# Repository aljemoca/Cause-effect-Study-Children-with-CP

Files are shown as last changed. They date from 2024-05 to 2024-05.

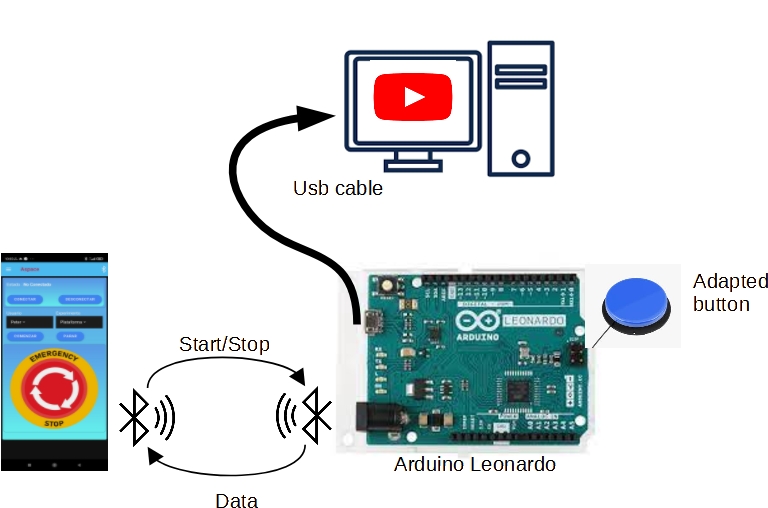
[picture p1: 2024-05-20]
Computer/AdaptedApplication.jpg

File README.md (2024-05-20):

# Cause-effect Study

 This project  contains the files needed to replicate all the elements (hardware/software) used to conduct an experiment to know the effect of mobility
 on cognitive skills in children with cerebral palsy. 

 Three main components are needed in this project:
 1) Platform (Explorer) that can be attached to a manual wheelchair and that can be operated by an adapted push button.
 2) A hardware that allows collecting data from typical cause-effect therapy programs. It consists of an Arduino-based switch-contrelled circuit that can control how long a video is played on a computer screen.
 3) A mobile application that allows controlling both hardware and collecting data for analysis.

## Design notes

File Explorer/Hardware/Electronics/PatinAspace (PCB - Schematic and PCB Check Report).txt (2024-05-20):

Schematic and PCB Check Report
------------------------------

Report Written:     Friday, May 28, 2021
Project Path:       C:\Users\ATC\Desktop\DISEÑO_PCB\DISEÑO_PCB\PatinAspace\PatinAspace.prj
Design Path:        C:\Users\ATC\Desktop\DISEÑO_PCB\DISEÑO_PCB\PatinAspace\PatinAspace.pcb
Design Title:       
Created:            25/05/2021 8:12:04
Last Saved:         28/05/2021 13:52:27
Editing Time:       4660 min
Units:              mm (precision 2)

Checking integrity of Schematic "C:\Users\ATC\Desktop\DISEÑO_PCB\DISEÑO_PCB\PatinAspace\PatinAspace.sch" with PCB "C:\Users\ATC\Desktop\DISEÑO_PCB\DISEÑO_PCB\PatinAspace\PatinAspace.pcb"
==========================================================================================================================================================================================

End Of Report.

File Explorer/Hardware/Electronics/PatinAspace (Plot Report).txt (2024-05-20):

Plot Report
-----------

Report Written:     Wednesday, November 24, 2021
Project Path:       C:\Users\ATC\Desktop\DISEÑO_PCB\DISEÑO_PCB\PatinAspace\PatinAspace.prj
Design Path:        C:\Users\ATC\Desktop\DISEÑO_PCB\DISEÑO_PCB\PatinAspace\PatinAspace.pcb
Design Title:       
Created:            25/05/2021 7:12:04
Last Saved:         02/06/2021 12:55:14
Editing Time:       4994 min
Units:              mm (precision 2)

Device Settings
===============

Gerber Settings
===============

    Leading zero suppression.
    G01 assumed throughout.
    Line termination <*> <CR> <LF>.
    3.5 format absolute inches.

    Format commands defined in Gerber file.
    Aperture table defined in Gerber file.
    Hardware arcs allowed.

Drill Settings
==============

    Excellon Format 2
    Format 3.5 absolute in mm.
    Zero suppression Leading

Plots Output
============

Gerber Output
=============

C:\Users\ATC\Desktop\DISEÑO_PCB\DISEÑO_PCB\PatinAspace\PatinAspace - Top Silkscreen.gbr

    Layers:
    ------------------
    Top Silkscreen

    D-Code Shape  (thou)
    -----------------------
    D12    Round 5.00
    D19    Round 12.00
    D22    Round 3.94

Gerber Output
=============

C:\Users\ATC\Desktop\DISEÑO_PCB\DISEÑO_PCB\PatinAspace\PatinAspace - Top Copper.gbr

    Layers:
    --------------
    Top Copper

    D-Code Shape  (thou)
    -------------------------------------------------------------
    D10    Round 11.81
    D13    Rounded Rectangle 60.00 X 60.00 X 0.00  Rotation 90
    D23    Round 25.20
    D24    Round 51.18
    D25    Round 15.00
    D78    Round 55.91
    D82    Round 60.00
    D99    Rectangle 60.00 X 60.00
    D100   Square 60.00

Gerber Output
=============

C:\Users\ATC\Desktop\DISEÑO_PCB\DISEÑO_PCB\PatinAspace\PatinAspace - Top Copper (Resist).gbr

    Layers:
    --------------
    Top Copper

    D-Code Shape  (thou)
    -------------------------------------------------------------
    D15    Rounded Rectangle 60.00 X 60.00 X 0.00  Rotation 90
    D91    Round 70.00
    D101   Rectangle 70.00 X 70.00
    D102   Square 70.00

Gerber Output
=============

C:\Users\ATC\Desktop\DISEÑO_PCB\DISEÑO_PCB\PatinAspace\PatinAspace - Top Copper (Paste).gbr

    Layers:
    --------------
    Top Copper

    D-Code Shape  (thou)
    -----------------------

Gerber Output
=============

C:\Users\ATC\Desktop\DISEÑO_PCB\DISEÑO_PCB\PatinAspace\PatinAspace - Bottom Copper.gbr

    Layers:
    -----------------
    Bottom Copper

    D-Code Shape  (thou)
    -------------------------------------------------------------
    D13    Rounded Rectangle 60.00 X 60.00 X 0.00  Rotation 90
    D23    Round 25.20
    D24    Round 51.18
    D25    Round 15.00
    D78    Round 55.91
    D82    Round 60.00
    D99    Rectangle 60.00 X 60.00
    D100   Square 60.00

Gerber Output
=============

C:\Users\ATC\Desktop\DISEÑO_PCB\DISEÑO_PCB\PatinAspace\PatinAspace - Bottom Copper (Resist).gbr

    Layers:
    -----------------
    Bottom Copper

    D-Code Shape  (thou)
    -------------------------------------------------------------
    D15    Rounded Rectangle 60.00 X 60.00 X 0.00  Rotation 90
    D91    Round 70.00
    D101   Rectangle 70.00 X 70.00
    D102   Square 70.00

Gerber Output
=============

C:\Users\ATC\Desktop\DISEÑO_PCB\DISEÑO_PCB\PatinAspace\PatinAspace - Bottom Copper (Paste).gbr

    Layers:
    -----------------
    Bottom Copper

    D-Code Shape  (thou)
    -----------------------

NC Drill Output
===============

C:\Users\ATC\Desktop\DISEÑO_PCB\DISEÑO_PCB\PatinAspace\PatinAspace - Drill Data - [Through Hole].drl

    Output:
    ---------------------------
    Plated Round Drill Holes
    Plated Slots

    Tool  Size       Count   ID
    ----------------------------------
    T001  0.40000 mm 31    E
    T002  0.70000 mm 48    G
    T003  0.80000 mm 76    F
    T004  0.85000 mm 68    B
    ----------------------------------
    Total            223
    ----------------------------------

C:\Users\ATC\Desktop\DISEÑO_PCB\DISEÑO_PCB\PatinAspace\PatinAspace - Drill Data - [Through Hole] (Unplated).drl

    Output:
    -----------------------------
    Unplated Round Drill Holes
    Unplated Slots

    Tool  Size Count   ID
    ----------------------------
    ----------------------------
    Total      0
    ----------------------------

Gerber Output
=============

C:\Users\ATC\Desktop\DISEÑO_PCB\DISEÑO_PCB\PatinAspace\PatinAspace - Drill Ident Drawing - [Through Hole].gbr

    Layers:
    ------------------
    [Through Hole]

Drill Ident Drawing
===================

    Drill Plated Size Shape ID
    -----------------------------------
    33    Y      100  Round B
    16    Y      100  Round E
    31    Y      100  Round F
    28    Y      100  Round G

    D-Code Shape  (thou)
    -----------------------
    D12    Round 5.00
    D18    Round 100.00

Gerber Output
=============

C:\Users\ATC\Desktop\DISEÑO_PCB\DISEÑO_PCB\PatinAspace\PatinAspace - board.gbr

    Layers:
    ------------------
    Board Outlines

    D-Code Shape  (thou)
    -----------------------
    D12    Round 5.00

Gerber Output
=============

C:\Users\ATC\Desktop\DISEÑO_PCB\DISEÑO_PCB\PatinAspace\PatinAspace - Botton Silkscreen.gbr

    Layers:
    ---------------------
    Bottom Silkscreen

    D-Code Shape  (thou)
    -----------------------

End Of Report.

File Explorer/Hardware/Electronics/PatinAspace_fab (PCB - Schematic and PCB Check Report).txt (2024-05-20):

Schematic and PCB Check Report
------------------------------

Report Written:     Thursday, June 10, 2021
Project Path:       C:\Users\ATC\Desktop\DISEÑO_PCB\DISEÑO_PCB\PatinAspace\PatinAspace_fab.prj
Design Path:        C:\Users\ATC\Desktop\DISEÑO_PCB\DISEÑO_PCB\PatinAspace\PatinAspace_fab.pcb
Design Title:       
Created:            25/05/2021 8:12:04
Last Saved:         10/06/2021 10:33:57
Editing Time:       5054 min
Units:              mm (precision 2)

Checking integrity of Schematic "C:\Users\ATC\Desktop\DISEÑO_PCB\DISEÑO_PCB\PatinAspace\PatinAspace_fab.sch" with PCB "C:\Users\ATC\Desktop\DISEÑO_PCB\DISEÑO_PCB\PatinAspace\PatinAspace_fab.pcb"
==================================================================================================================================================================================================

The PCB and Schematic designs do not match.
To bring them into line, you will need to make the following changes to the PCB design:

Component 'HC-SR04-CONNECTOR' package 'DIL' in PCB is newer version than Schematic, use Update Component to correct this.
Component '2WP' package 'DSC' in PCB is newer version than Schematic, use Update Component to correct this.

End Of Report.

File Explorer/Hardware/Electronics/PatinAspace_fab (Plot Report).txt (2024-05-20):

Plot Report
-----------

Report Written:     Thursday, July 08, 2021
Project Path:       C:\Users\ATC\Desktop\DISEÑO_PCB\DISEÑO_PCB\PatinAspace\PatinAspace_fab.prj
Design Path:        C:\Users\ATC\Desktop\DISEÑO_PCB\DISEÑO_PCB\PatinAspace\PatinAspace_fab.pcb
Design Title:       
Created:            25/05/2021 8:12:04
Last Saved:         18/06/2021 12:55:20
Editing Time:       5095 min
Units:              mm (precision 2)

Device Settings
===============

Gerber Settings
===============

    Leading zero suppression.
    G01 assumed throughout.
    Line termination <*> <CR> <LF>.
    3.5 format absolute inches.

    Format commands defined in Gerber file.
    Aperture table defined in Gerber file.
    Hardware arcs allowed.

Drill Settings
==============

    Excellon Format 2
    Format 3.5 absolute in mm.
    Zero suppression Leading

Plots Output
============

Gerber Output
=============

C:\Users\ATC\Desktop\DISEÑO_PCB\DISEÑO_PCB\PatinAspace\PatinAspace_fab - Top Silkscreen.gbr

    Layers:
    ------------------
    Top Silkscreen

    D-Code Shape  (thou)
    -----------------------
    D10    Round 11.81
    D12    Round 5.00
    D19    Round 12.00
    D22    Round 3.94

Gerber Output
=============

C:\Users\ATC\Desktop\DISEÑO_PCB\DISEÑO_PCB\PatinAspace\PatinAspace_fab - Top Copper.gbr

    Layers:
    --------------
    Top Copper

    D-Code Shape  (thou)
    -------------------------------------------------------------
    D23    Round 25.20
    D24    Round 51.18
    D25    Round 15.00
    D26    Rounded Rectangle 59.06 X 59.06 X 0.00  Rotation 90
    D27    Rectangle 59.06 X 59.06
    D28    Round 59.06
    D29    Square 59.06

Gerber Output
=============

C:\Users\ATC\Desktop\DISEÑO_PCB\DISEÑO_PCB\PatinAspace\PatinAspace_fab - Top Copper (Resist).gbr

    Layers:
    --------------
    Top Copper

    D-Code Shape  (thou)
    -------------------------------------------------------------
    D72    Rounded Rectangle 59.06 X 59.06 X 0.00  Rotation 90
    D73    Rectangle 69.06 X 69.06
    D74    Round 69.06
    D75    Square 69.06

Gerber Output
=============

C:\Users\ATC\Desktop\DISEÑO_PCB\DISEÑO_PCB\PatinAspace\PatinAspace_fab - Top Copper (Paste).gbr

    Layers:
    --------------
    Top Copper

    D-Code Shape  (thou)
    -----------------------

Gerber Output
=============

C:\Users\ATC\Desktop\DISEÑO_PCB\DISEÑO_PCB\PatinAspace\PatinAspace_fab - Bottom Copper.gbr

    Layers:
    -----------------
    Bottom Copper

    D-Code Shape  (thou)
    -------------------------------------------------------------
    D12    Round 5.00
    D23    Round 25.20
    D24    Round 51.18
    D25    Round 15.00
    D26    Rounded Rectangle 59.06 X 59.06 X 0.00  Rotation 90
    D27    Rectangle 59.06 X 59.06
    D28    Round 59.06
    D29    Square 59.06
    D76    Round 10.00

Gerber Output
=============

C:\Users\ATC\Desktop\DISEÑO_PCB\DISEÑO_PCB\PatinAspace\PatinAspace_fab - Bottom Copper (Resist).gbr

    Layers:
    -----------------
    Bottom Copper

    D-Code Shape  (thou)
    -------------------------------------------------------------
    D72    Rounded Rectangle 59.06 X 59.06 X 0.00  Rotation 90
    D73    Rectangle 69.06 X 69.06
    D74    Round 69.06
    D75    Square 69.06

Gerber Output
=============

C:\Users\ATC\Desktop\DISEÑO_PCB\DISEÑO_PCB\PatinAspace\PatinAspace_fab - Bottom Copper (Paste).gbr

    Layers:
    -----------------
    Bottom Copper

    D-Code Shape  (thou)
    -----------------------

NC Drill Output
===============

C:\Users\ATC\Desktop\DISEÑO_PCB\DISEÑO_PCB\PatinAspace\PatinAspace_fab - Drill Data - [Through Hole].drl

    Output:
    ---------------------------
    Plated Round Drill Holes
    Plated Slots

    Tool  Size       Count   ID
    ----------------------------------
    T001  0.60000 mm 33    D
    T002  0.80000 mm 124   F
    T003  0.90000 mm 16    H
    T004  1.02000 mm 52    I
    ----------------------------------
    Total            225
    ----------------------------------

C:\Users\ATC\Desktop\DISEÑO_PCB\DISEÑO_PCB\PatinAspace\PatinAspace_fab - Drill Data - [Through Hole] (Unplated).drl

    Output:
    -----------------------------
    Unplated Round Drill Holes
    Unplated Slots

    Tool  Size Count   ID
    ----------------------------
    ----------------------------
    Total      0
    ----------------------------

Gerber Output
=============

C:\Users\ATC\Desktop\DISEÑO_PCB\DISEÑO_PCB\PatinAspace\PatinAspace_fab - Drill Ident Drawing - [Through Hole].gbr

    Layers:
    ------------------
    [Through Hole]

Drill Ident Drawing
===================

    Drill Plated Size Shape ID
    -----------------------------------
    24    Y      100  Round D
    31    Y      100  Round F
    35    Y      100  Round H
    40    Y      100  Round I

    D-Code Shape  (thou)
    -----------------------
    D12    Round 5.00
    D18    Round 100.00

Gerber Output
=============

C:\Users\ATC\Desktop\DISEÑO_PCB\DISEÑO_PCB\PatinAspace\PatinAspace_fab - board_outline.gbr

    Layers:
    ------------------
    Board Outlines

    D-Code Shape  (thou)
    -----------------------
    D12    Round 5.00

End Of Report.

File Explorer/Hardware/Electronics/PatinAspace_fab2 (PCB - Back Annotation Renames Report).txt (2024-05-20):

Back Annotation Renames Report
------------------------------

Report Written:     Thursday, June 23, 2022
Project Path:       C:\Users\ATC\Desktop\DISEÑO_PCB\DISEÑO_PCB\PatinAspace2\PatinAspace_fab.prj
Design Path:        C:\Users\ATC\Desktop\DISEÑO_PCB\DISEÑO_PCB\PatinAspace2\PatinAspace_fab2.pcb
Design Title:       
Created:            25/05/2021 8:12:04
Last Saved:         23/06/2022 11:40:32
Editing Time:       6887 min
Units:              mm (precision 2)

Outstanding PCB renames awaiting back annotation to the Schematics design.

Rename Net from "enaRight" to "enaLeft1".
Rename Net from "enaLeft" to "enaRight".
Rename Net from "enaLeft1" to "enaLeft".

End Of Report.

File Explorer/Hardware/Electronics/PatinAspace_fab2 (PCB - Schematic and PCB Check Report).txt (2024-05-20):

Schematic and PCB Check Report
------------------------------

Report Written:     Thursday, June 23, 2022
Project Path:       C:\Users\ATC\Desktop\DISEÑO_PCB\DISEÑO_PCB\PatinAspace2\PatinAspace_fab.prj
Design Path:        C:\Users\ATC\Desktop\DISEÑO_PCB\DISEÑO_PCB\PatinAspace2\PatinAspace_fab2.pcb
Design Title:       
Created:            25/05/2021 8:12:04
Last Saved:         23/06/2022 11:47:56
Editing Time:       6896 min
Units:              mm (precision 2)

Checking integrity of Schematic "C:\Users\ATC\Desktop\DISEÑO_PCB\DISEÑO_PCB\PatinAspace2\PatinAspace_fab2.sch" with PCB "C:\Users\ATC\Desktop\DISEÑO_PCB\DISEÑO_PCB\PatinAspace2\PatinAspace_fab2.pcb"
======================================================================================================================================================================================================

The PCB and Schematic designs do not match.
To bring them into line, you will need to make the following changes to the PCB design:

Component '2WP' package 'DSC' in PCB is newer version than Schematic, use Update Component to correct this.
Component 'BORNA_TRIPLE' package 'DIL' in PCB is newer version than Schematic, use Update Component to correct this.
Component 'BORNA_DOBLE' package 'DIL' in PCB is newer version than Schematic, use Update Component to correct this.

End Of Report.

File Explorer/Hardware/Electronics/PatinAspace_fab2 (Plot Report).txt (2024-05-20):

Plot Report
-----------

Report Written:     Friday, June 10, 2022
Project Path:       C:\Users\ATC\Desktop\DISEÑO_PCB\DISEÑO_PCB\PatinAspace2\PatinAspace_fab.prj
Design Path:        C:\Users\ATC\Desktop\DISEÑO_PCB\DISEÑO_PCB\PatinAspace2\PatinAspace_fab2.pcb
Design Title:       
Created:            25/05/2021 8:12:04
Last Saved:         10/06/2022 10:48:15
Editing Time:       6743 min
Units:              mm (precision 2)

Device Settings
===============

Gerber Settings
===============

    Leading zero suppression.
    G01 assumed throughout.
    Line termination <*> <CR> <LF>.
    3.5 format absolute inches.

    Format commands defined in Gerber file.
    Aperture table defined in Gerber file.
    Hardware arcs allowed.

Drill Settings
==============

    Excellon Format 2
    Format 3.5 absolute in mm.
    Zero suppression Leading

Plots Output
============

Gerber Output
=============

C:\Users\ATC\Desktop\DISEÑO_PCB\DISEÑO_PCB\PatinAspace2\PatinAspace_fab2 - Top Silkscreen.gbr

    Layers:
    ------------------
    Top Silkscreen

    D-Code Shape  (thou)
    -----------------------
    D10    Round 11.81
    D12    Round 5.00
    D19    Round 12.00
    D22    Round 3.94

Gerber Output
=============

C:\Users\ATC\Desktop\DISEÑO_PCB\DISEÑO_PCB\PatinAspace2\PatinAspace_fab2 - Top Copper.gbr

    Layers:
    --------------
    Top Copper

    D-Code Shape  (thou)
    -------------------------------------------------------------
    D23    Round 25.20
    D25    Round 15.00
    D26    Rounded Rectangle 59.06 X 59.06 X 0.00  Rotation 90
    D28    Round 59.06
    D29    Square 59.06
    D88    Round 98.43
    D106   Round 39.37
    D107   Round 137.80

Gerber Output
=============

C:\Users\ATC\Desktop\DISEÑO_PCB\DISEÑO_PCB\PatinAspace2\PatinAspace_fab2 - Top Copper (Resist).gbr

    Layers:
    --------------
    Top Copper

    D-Code Shape  (thou)
    -------------------------------------------------------------
    D72    Rounded Rectangle 59.06 X 59.06 X 0.00  Rotation 90
    D74    Round 69.06
    D75    Square 69.06
    D97    Round 108.43
    D108   Round 147.80

Gerber Output
=============

C:\Users\ATC\Desktop\DISEÑO_PCB\DISEÑO_PCB\PatinAspace2\PatinAspace_fab2 - Top Copper (Paste).gbr

    Layers:
    --------------
    Top Copper

    D-Code Shape  (thou)
    -----------------------

Gerber Output
=============

C:\Users\ATC\Desktop\DISEÑO_PCB\DISEÑO_PCB\PatinAspace2\PatinAspace_fab2 - Bottom Copper.gbr

    Layers:
    -----------------
    Bottom Copper

    D-Code Shape  (thou)
    -------------------------------------------------------------
    D12    Round 5.00
    D23    Round 25.20
    D25    Round 15.00
    D26    Rounded Rectangle 59.06 X 59.06 X 0.00  Rotation 90
    D28    Round 59.06
    D29    Square 59.06
    D76    Round 10.00
    D88    Round 98.43
    D106   Round 39.37
    D107   Round 137.80

Gerber Output
=============

C:\Users\ATC\Desktop\DISEÑO_PCB\DISEÑO_PCB\PatinAspace2\PatinAspace_fab2 - Bottom Copper (Resist).gbr

    Layers:
    -----------------
    Bottom Copper

    D-Code Shape  (thou)
    -------------------------------------------------------------
    D72    Rounded Rectangle 59.06 X 59.06 X 0.00  Rotation 90
    D74    Round 69.06
    D75    Square 69.06
    D97    Round 108.43
    D108   Round 147.80

Gerber Output
=============

C:\Users\ATC\Desktop\DISEÑO_PCB\DISEÑO_PCB\PatinAspace2\PatinAspace_fab2 - Bottom Copper (Paste).gbr

    Layers:
    -----------------
    Bottom Copper

    D-Code Shape  (thou)
    -----------------------

Gerber Output
=============

C:\Users\ATC\Desktop\DISEÑO_PCB\DISEÑO_PCB\PatinAspace2\PatinAspace_fab2 - Bottom Silkscreen.gbr

    Layers:
    ---------------------
    Bottom Silkscreen

    D-Code Shape  (thou)
    -----------------------
    D10    Round 11.81

NC Drill Output
===============

C:\Users\ATC\Desktop\DISEÑO_PCB\DISEÑO_PCB\PatinAspace2\PatinAspace_fab2 - Drill Data - [Through Hole].drl

    Output:
    ---------------------------
    Plated Round Drill Holes
    Plated Slots

    Tool  Size       Count   ID
    ----------------------------------
    T001  0.60000 mm 117   D
    T002  0.80000 mm 170   F
    T003  1.02000 mm 10    I
    T004  1.40000 mm 61    R
    T005  3.00000 mm 5     S
    ----------------------------------
    Total            363
    ----------------------------------

C:\Users\ATC\Desktop\DISEÑO_PCB\DISEÑO_PCB\PatinAspace2\PatinAspace_fab2 - Drill Data - [Through Hole] (Unplated).drl

    Output:
    -----------------------------
    Unplated Round Drill Holes
    Unplated Slots

    Tool  Size Count   ID
    ----------------------------
    ----------------------------
    Total      0
    ----------------------------

Gerber Output
=============

C:\Users\ATC\Desktop\DISEÑO_PCB\DISEÑO_PCB\PatinAspace2\PatinAspace_fab2 - Drill Ident Drawing - [Through Hole].gbr

    Layers:
    ------------------
    [Through Hole]

Drill Ident Drawing
===================

    Drill Plated Size Shape ID
    -----------------------------------
    24    Y      100  Round D
    31    Y      100  Round F
    40    Y      100  Round I
    55    Y      100  Round R
    118   Y      100  Round S

    D-Code Shape  (thou)
    -----------------------
    D12    Round 5.00
    D18    Round 100.00

Gerber Output
=============

C:\Users\ATC\Desktop\DISEÑO_PCB\DISEÑO_PCB\PatinAspace2\PatinAspace_fab2 - border.gbr

    Layers:
    ------------------
    Board Outlines

    D-Code Shape  (thou)
    -----------------------
    D12    Round 5.00

End Of Report.

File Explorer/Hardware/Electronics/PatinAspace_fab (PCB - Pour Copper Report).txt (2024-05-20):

Pour Copper Report
------------------

Report Written:     Friday, June 18, 2021
Project Path:       C:\Users\ATC\Desktop\DISEÑO_PCB\DISEÑO_PCB\PatinAspace\PatinAspace_fab.prj
Design Path:        C:\Users\ATC\Desktop\DISEÑO_PCB\DISEÑO_PCB\PatinAspace\PatinAspace_fab.pcb
Design Title:       
Created:            25/05/2021 8:12:04
Last Saved:         10/06/2021 11:15:35
Editing Time:       5089 min
Units:              mm (precision 2)

End Of Report.

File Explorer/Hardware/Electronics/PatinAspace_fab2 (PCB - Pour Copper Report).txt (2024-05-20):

Pour Copper Report
------------------

Report Written:     Friday, June 10, 2022
Project Path:       C:\Users\ATC\Desktop\DISEÑO_PCB\DISEÑO_PCB\PatinAspace2\PatinAspace_fab.prj
Design Path:        C:\Users\ATC\Desktop\DISEÑO_PCB\DISEÑO_PCB\PatinAspace2\PatinAspace_fab2.pcb
Design Title:       
Created:            25/05/2021 8:12:04
Last Saved:         10/06/2022 10:44:31
Editing Time:       6741 min
Units:              mm (precision 2)

U1.28 at 478.27,362.26 on layer Bottom Copper has no thermal spokes
R7.1 at 528.80,338.90 on layer Bottom Copper has no thermal spokes

End Of Report.

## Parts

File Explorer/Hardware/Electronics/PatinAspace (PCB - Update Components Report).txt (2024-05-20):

Update Components Report
------------------------

Report Written:     Friday, May 28, 2021
Project Path:       C:\Users\ATC\Desktop\DISEÑO_PCB\DISEÑO_PCB\PatinAspace\PatinAspace.prj
Design Path:        C:\Users\ATC\Desktop\DISEÑO_PCB\DISEÑO_PCB\PatinAspace\PatinAspace.pcb
Design Title:       
Created:            25/05/2021 8:12:04
Last Saved:         28/05/2021 10:14:13
Editing Time:       4446 min
Units:              mm (precision 2)

Library Files:
==============

C:\Users\Public\Documents\DesignSpark PCB 9.0\Library\User\User.cml
C:\Users\Public\Documents\DesignSpark PCB 9.0\Library\Default\DesignSpark.cml
C:\Users\Public\Documents\DesignSpark PCB 9.0\Library\Default\ltspice.cml
C:\Users\Public\Documents\DesignSpark PCB 9.0\Library\Default\XSpice.cml
C:\Users\Public\Documents\DesignSpark PCB 9.0\Library\Picaxe\PICAXE_Create_Components.cml
C:\Users\Public\Documents\DesignSpark PCB 9.0\Library\Picaxe\PICAXE_Create_PICAXE.cml
C:\Users\Public\Documents\DesignSpark PCB 9.0\Library\3m.cml
C:\Users\Public\Documents\DesignSpark PCB 9.0\Library\74hc.cml
C:\Users\Public\Documents\DesignSpark PCB 9.0\Library\74hct.cml
C:\Users\Public\Documents\DesignSpark PCB 9.0\Library\74ls.cml
C:\Users\Public\Documents\DesignSpark PCB 9.0\Library\4000.cml
C:\Users\Public\Documents\DesignSpark PCB 9.0\Library\actel.cml
C:\Users\Public\Documents\DesignSpark PCB 9.0\Library\ad.cml
C:\Users\Public\Documents\DesignSpark PCB 9.0\Library\adsp.cml
C:\Users\Public\Documents\DesignSpark PCB 9.0\Library\altera.cml
C:\Users\Public\Documents\DesignSpark PCB 9.0\Library\alteracyclone.cml
C:\Users\Public\Documents\DesignSpark PCB 9.0\Library\amp.cml
C:\Users\Public\Documents\DesignSpark PCB 9.0\Library\atmel.cml
C:\Users\Public\Documents\DesignSpark PCB 9.0\Library\atmel8051.cml
C:\Users\Public\Documents\DesignSpark PCB 9.0\Library\atmelarm.cml
C:\Users\Public\Documents\DesignSpark PCB 9.0\Library\atmelatsam7.cml
C:\Users\Public\Documents\DesignSpark PCB 9.0\Library\atmelavr.cml
C:\Users\Public\Documents\DesignSpark PCB 9.0\Library\avx.cml
C:\Users\Public\Documents\DesignSpark PCB 9.0\Library\capacitor.cml
C:\Users\Public\Documents\DesignSpark PCB 9.0\Library\coldfire.cml
C:\Users\Public\Documents\DesignSpark PCB 9.0\Library\connector.cml
C:\Users\Public\Documents\DesignSpark PCB 9.0\Library\csm.cml
C:\Users\Public\Documents\DesignSpark PCB 9.0\Library\cypress.cml
C:\Users\Public\Documents\DesignSpark PCB 9.0\Library\diode.cml
C:\Users\Public\Documents\DesignSpark PCB 9.0\Library\discrete.cml
C:\Users\Public\Documents\DesignSpark PCB 9.0\Library\dsm.cml
C:\Users\Public\Documents\DesignSpark PCB 9.0\Library\fairchild.cml
C:\Users\Public\Documents\DesignSpark PCB 9.0\Library\fairchild1.cml
C:\Users\Public\Documents\DesignSpark PCB 9.0\Library\fairchildacex.cml
C:\Users\Public\Documents\DesignSpark PCB 9.0\Library\fci.cml
C:\Users\Public\Documents\DesignSpark PCB 9.0\Library\fuse.cml
C:\Users\Public\Documents\DesignSpark PCB 9.0\Library\hamlin.cml
C:\Users\Public\Documents\DesignSpark PCB 9.0\Library\hybrid.cml
C:\Users\Public\Documents\DesignSpark PCB 9.0\Library\infineontc116x.cml
C:\Users\Public\Documents\DesignSpark PCB 9.0\Library\intel8051.cml
C:\Users\Public\Documents\DesignSpark PCB 9.0\Library\ir.cml
C:\Users\Public\Documents\DesignSpark PCB 9.0\Library\lattice.cml
C:\Users\Public\Documents\DesignSpark PCB 9.0\Library\lt.cml
C:\Users\Public\Documents\DesignSpark PCB 9.0\Library\ltspice.cml
C:\Users\Public\Documents\DesignSpark PCB 9.0\Library\luminarycortex.cml
C:\Users\Public\Documents\DesignSpark PCB 9.0\Library\maxim.cml
C:\Users\Public\Documents\DesignSpark PCB 9.0\Library\maxim8051.cml
C:\Users\Public\Documents\DesignSpark PCB 9.0\Library\maximmp.cml
C:\Users\Public\Documents\DesignSpark PCB 9.0\Library\mc68hc.cml
C:\Users\Public\Documents\DesignSpark PCB 9.0\Library\microchip.cml
C:\Users\Public\Documents\DesignSpark PCB 9.0\Library\microchippic.cml
C:\Users\Public\Documents\DesignSpark PCB 9.0\Library\molex.cml
C:\Users\Public\Documents\DesignSpark PCB 9.0\Library\msp430.cml
C:\Users\Public\Documents\DesignSpark PCB 9.0\Library\murata.cml
C:\Users\Public\Documents\DesignSpark PCB 9.0\Library\natsemi.cml
C:\Users\Public\Documents\DesignSpark PCB 9.0\Library\nxp-lpc32x0.cml
C:\Users\Public\Documents\DesignSpark PCB 9.0\Library\omron.cml
C:\Users\Public\Documents\DesignSpark PCB 9.0\Library\onsemi.cml
C:\Users\Public\Documents\DesignSpark PCB 9.0\Library\opamps.cml
C:\Users\Public\Documents\DesignSpark PCB 9.0\Library\pcb.cml
C:\Users\Public\Documents\DesignSpark PCB 9.0\Library\philips80c51.cml
C:\Users\Public\Documents\DesignSpark PCB 9.0\Library\philipsarm.cml
C:\Users\Public\Documents\DesignSpark PCB 9.0\Library\philipsp89.cml
C:\Users\Public\Documents\DesignSpark PCB 9.0\Library\philipsxa.cml
C:\Users\Public\Documents\DesignSpark PCB 9.0\Library\picaxe.cml
C:\Users\Public\Documents\DesignSpark PCB 9.0\Library\powerpc.cml
C:\Users\Public\Documents\DesignSpark PCB 9.0\Library\qbsm.cml
C:\Users\Public\Documents\DesignSpark PCB 9.0\Library\qcsm.cml
C:\Users\Public\Documents\DesignSpark PCB 9.0\Library\qsm.cml
C:\Users\Public\Documents\DesignSpark PCB 9.0\Library\quicklogic.cml
C:\Users\Public\Documents\DesignSpark PCB 9.0\Library\relay.cml
C:\Users\Public\Documents\DesignSpark PCB 9.0\Library\renesasr8c.cml
C:\Users\Public\Documents\DesignSpark PCB 9.0\Library\resistor.cml
C:\Users\Public\Documents\DesignSpark PCB 9.0\Library\rfmicro.cml
C:\Users\Public\Documents\DesignSpark PCB 9.0\Library\schema.cml
C:\Users\Public\Documents\DesignSpark PCB 9.0\Library\sm.cml
C:\Users\Public\Documents\DesignSpark PCB 9.0\Library\sonycx.cml
C:\Users\Public\Documents\DesignSpark PCB 9.0\Library\st-arm7.cml
C:\Users\Public\Documents\DesignSpark PCB 9.0\Library\st.cml
C:\Users\Public\Documents\DesignSpark PCB 9.0\Library\testpoint.cml
C:\Users\Public\Documents\DesignSpark PCB 9.0\Library\ti.cml
C:\Users\Public\Documents\DesignSpark PCB 9.0\Library\tms320.cml
C:\Users\Public\Documents\DesignSpark PCB 9.0\Library\tms470.cml
C:\Users\Public\Documents\DesignSpark PCB 9.0\Library\toshibatmp86.cml
C:\Users\Public\Documents\DesignSpark PCB 9.0\Library\trans.cml
C:\Users\Public\Documents\DesignSpark PCB 9.0\Library\transistor.cml
C:\Users\Public\Documents\DesignSpark PCB 9.0\Library\vishay.cml
C:\Users\Public\Documents\DesignSpark PCB 9.0\Library\xilinx.cml
C:\Users\Public\Documents\DesignSpark PCB 9.0\Library\XSpice.cml
C:\Users\Public\Documents\DesignSpark PCB 9.0\Library\zilog.cml

Selected items to be updated:
=============================

Components:
===========

    (None) 

Symbols:
========

    (None) 

Additional items to be updated:
===============================

Components:
===========

    (None) 

Symbols:
========

    (None) 

Selected items not to be updated  (Same version as library)
===========================================================

Components:
===========

2WP (DSC)
BC547 (DSC)
BRUSHLESS_CONTROLER_CONNECTOR (DIL)
CONN_SIL_4 (DSC)
DFPlayer_Mini (DIL)
HC-05_CONNECTOR (DIL)
HC-SR04-CONNECTOR (DIL)
NUCLEOF446 (DIL)
R (DSC)

Symbols:
========

2                             C:\Users\Public\Documents\DesignSpark PCB 9.0\Library\Default\DesignSpark.psl
4                             C:\Users\Public\Documents\DesignSpark PCB 9.0\Library\Default\DesignSpark.psl
BRUSHLESS_CONTROLER_CONNECTOR C:\Users\Public\Documents\DesignSpark PCB 9.0\Library\User\User.psl
DFPlayer_Mini                 C:\Users\Public\Documents\DesignSpark PCB 9.0\Library\User\User.psl
DISC04                        C:\Users\Public\Documents\DesignSpark PCB 9.0\Library\Default\DesignSpark.psl
HC-05_CONNECTOR               C:\Users\Public\Documents\DesignSpark PCB 9.0\Library\User\User.psl
HC-SR04-CONNECTOR             C:\Users\Public\Documents\DesignSpark PCB 9.0\Library\User\User.psl
Nucleof446                    C:\Users\Public\Documents\DesignSpark PCB 9.0\Library\User\User.psl
TO92A                         C:\Users\Public\Documents\DesignSpark PCB 9.0\Library\Default\DesignSpark.psl

Update Components Summary
=========================

Updating all components.
Update component values
Update component value positions
(Remove pad style exceptions on updated components)
	Selected for update:			   9  Components
						   9  Symbols
	Selected items to be updated:		   0  Components
						   0  Symbols
	Additional items to be updated:		   0  Components
						   0  Symbols
	Selected items NOT to be updated:	   9  Components
	  (Same version as library)		   9  Symbols

End Of Report.

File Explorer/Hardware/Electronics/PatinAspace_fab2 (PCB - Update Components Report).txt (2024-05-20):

Update Components Report
------------------------

Report Written:     Friday, May 20, 2022
Project Path:       C:\Users\ATC\Desktop\DISEÑO_PCB\DISEÑO_PCB\PatinAspace2\PatinAspace_fab.prj
Design Path:        C:\Users\ATC\Desktop\DISEÑO_PCB\DISEÑO_PCB\PatinAspace2\PatinAspace_fab2.pcb
Design Title:       
Created:            25/05/2021 8:12:04
Last Saved:         20/05/2022 13:44:01
Editing Time:       5507 min
Units:              mm (precision 2)

Library Files:
==============

C:\Users\Public\Documents\DesignSpark PCB 9.0\Library\User\User.cml
C:\Users\Public\Documents\DesignSpark PCB 9.0\Library\Default\DesignSpark.cml
C:\Users\Public\Documents\DesignSpark PCB 9.0\Library\Default\ltspice.cml
C:\Users\Public\Documents\DesignSpark PCB 9.0\Library\Default\XSpice.cml
C:\Users\Public\Documents\DesignSpark PCB 9.0\Library\Picaxe\PICAXE_Create_Components.cml
C:\Users\Public\Documents\DesignSpark PCB 9.0\Library\Picaxe\PICAXE_Create_PICAXE.cml
C:\Users\Public\Documents\DesignSpark PCB 9.0\Library\3m.cml
C:\Users\Public\Documents\DesignSpark PCB 9.0\Library\74hc.cml
C:\Users\Public\Documents\DesignSpark PCB 9.0\Library\74hct.cml
C:\Users\Public\Documents\DesignSpark PCB 9.0\Library\74ls.cml
C:\Users\Public\Documents\DesignSpark PCB 9.0\Library\4000.cml
C:\Users\Public\Documents\DesignSpark PCB 9.0\Library\actel.cml
C:\Users\Public\Documents\DesignSpark PCB 9.0\Library\ad.cml
C:\Users\Public\Documents\DesignSpark PCB 9.0\Library\adsp.cml
C:\Users\Public\Documents\DesignSpark PCB 9.0\Library\altera.cml
C:\Users\Public\Documents\DesignSpark PCB 9.0\Library\alteracyclone.cml
C:\Users\Public\Documents\DesignSpark PCB 9.0\Library\amp.cml
C:\Users\Public\Documents\DesignSpark PCB 9.0\Library\atmel.cml
C:\Users\Public\Documents\DesignSpark PCB 9.0\Library\atmel8051.cml
C:\Users\Public\Documents\DesignSpark PCB 9.0\Library\atmelarm.cml
C:\Users\Public\Documents\DesignSpark PCB 9.0\Library\atmelatsam7.cml
C:\Users\Public\Documents\DesignSpark PCB 9.0\Library\atmelavr.cml
C:\Users\Public\Documents\DesignSpark PCB 9.0\Library\avx.cml
C:\Users\Public\Documents\DesignSpark PCB 9.0\Library\capacitor.cml
C:\Users\Public\Documents\DesignSpark PCB 9.0\Library\coldfire.cml
C:\Users\Public\Documents\DesignSpark PCB 9.0\Library\connector.cml
C:\Users\Public\Documents\DesignSpark PCB 9.0\Library\csm.cml
C:\Users\Public\Documents\DesignSpark PCB 9.0\Library\cypress.cml
C:\Users\Public\Documents\DesignSpark PCB 9.0\Library\diode.cml
C:\Users\Public\Documents\DesignSpark PCB 9.0\Library\discrete.cml
C:\Users\Public\Documents\DesignSpark PCB 9.0\Library\dsm.cml
C:\Users\Public\Documents\DesignSpark PCB 9.0\Library\fairchild.cml
C:\Users\Public\Documents\DesignSpark PCB 9.0\Library\fairchild1.cml
C:\Users\Public\Documents\DesignSpark PCB 9.0\Library\fairchildacex.cml
C:\Users\Public\Documents\DesignSpark PCB 9.0\Library\fci.cml
C:\Users\Public\Documents\DesignSpark PCB 9.0\Library\fuse.cml
C:\Users\Public\Documents\DesignSpark PCB 9.0\Library\hamlin.cml
C:\Users\Public\Documents\DesignSpark PCB 9.0\Library\hybrid.cml
C:\Users\Public\Documents\DesignSpark PCB 9.0\Library\infineontc116x.cml
C:\Users\Public\Documents\DesignSpark PCB 9.0\Library\intel8051.cml
C:\Users\Public\Documents\DesignSpark PCB 9.0\Library\ir.cml
C:\Users\Public\Documents\DesignSpark PCB 9.0\Library\lattice.cml
C:\Users\Public\Documents\DesignSpark PCB 9.0\Library\lt.cml
C:\Users\Public\Documents\DesignSpark PCB 9.0\Library\ltspice.cml
C:\Users\Public\Documents\DesignSpark PCB 9.0\Library\luminarycortex.cml
C:\Users\Public\Documents\DesignSpark PCB 9.0\Library\maxim.cml
C:\Users\Public\Documents\DesignSpark PCB 9.0\Library\maxim8051.cml
C:\Users\Public\Documents\DesignSpark PCB 9.0\Library\maximmp.cml
C:\Users\Public\Documents\DesignSpark PCB 9.0\Library\mc68hc.cml
C:\Users\Public\Documents\DesignSpark PCB 9.0\Library\microchip.cml
C:\Users\Public\Documents\DesignSpark PCB 9.0\Library\microchippic.cml
C:\Users\Public\Documents\DesignSpark PCB 9.0\Library\molex.cml
C:\Users\Public\Documents\DesignSpark PCB 9.0\Library\msp430.cml
C:\Users\Public\Documents\DesignSpark PCB 9.0\Library\murata.cml
C:\Users\Public\Documents\DesignSpark PCB 9.0\Library\natsemi.cml
C:\Users\Public\Documents\DesignSpark PCB 9.0\Library\nxp-lpc32x0.cml
C:\Users\Public\Documents\DesignSpark PCB 9.0\Library\omron.cml
C:\Users\Public\Documents\DesignSpark PCB 9.0\Library\onsemi.cml
C:\Users\Public\Documents\DesignSpark PCB 9.0\Library\opamps.cml
C:\Users\Public\Documents\DesignSpark PCB 9.0\Library\pcb.cml
C:\Users\Public\Documents\DesignSpark PCB 9.0\Library\philips80c51.cml
C:\Users\Public\Documents\DesignSpark PCB 9.0\Library\philipsarm.cml
C:\Users\Public\Documents\DesignSpark PCB 9.0\Library\philipsp89.cml
C:\Users\Public\Documents\DesignSpark PCB 9.0\Library\philipsxa.cml
C:\Users\Public\Documents\DesignSpark PCB 9.0\Library\picaxe.cml
C:\Users\Public\Documents\DesignSpark PCB 9.0\Library\powerpc.cml
C:\Users\Public\Documents\DesignSpark PCB 9.0\Library\qbsm.cml
C:\Users\Public\Documents\DesignSpark PCB 9.0\Library\qcsm.cml
C:\Users\Public\Documents\DesignSpark PCB 9.0\Library\qsm.cml
C:\Users\Public\Documents\DesignSpark PCB 9.0\Library\quicklogic.cml
C:\Users\Public\Documents\DesignSpark PCB 9.0\Library\relay.cml
C:\Users\Public\Documents\DesignSpark PCB 9.0\Library\renesasr8c.cml
C:\Users\Public\Documents\DesignSpark PCB 9.0\Library\resistor.cml
C:\Users\Public\Documents\DesignSpark PCB 9.0\Library\rfmicro.cml
C:\Users\Public\Documents\DesignSpark PCB 9.0\Library\schema.cml
C:\Users\Public\Documents\DesignSpark PCB 9.0\Library\sm.cml
C:\Users\Public\Documents\DesignSpark PCB 9.0\Library\sonycx.cml
C:\Users\Public\Documents\DesignSpark PCB 9.0\Library\st-arm7.cml
C:\Users\Public\Documents\DesignSpark PCB 9.0\Library\st.cml
C:\Users\Public\Documents\DesignSpark PCB 9.0\Library\testpoint.cml
C:\Users\Public\Documents\DesignSpark PCB 9.0\Library\ti.cml
C:\Users\Public\Documents\DesignSpark PCB 9.0\Library\tms320.cml
C:\Users\Public\Documents\DesignSpark PCB 9.0\Library\tms470.cml
C:\Users\Public\Documents\DesignSpark PCB 9.0\Library\toshibatmp86.cml
C:\Users\Public\Documents\DesignSpark PCB 9.0\Library\trans.cml
C:\Users\Public\Documents\DesignSpark PCB 9.0\Library\transistor.cml
C:\Users\Public\Documents\DesignSpark PCB 9.0\Library\vishay.cml
C:\Users\Public\Documents\DesignSpark PCB 9.0\Library\xilinx.cml
C:\Users\Public\Documents\DesignSpark PCB 9.0\Library\XSpice.cml
C:\Users\Public\Documents\DesignSpark PCB 9.0\Library\zilog.cml

Selected items to be updated:
=============================

Components:
===========

    (None) 

Symbols:
========

    (None) 

Reference Names:
================

    (None) 

Additional items to be updated:
===============================

Components:
===========

    (None) 

Symbols:
========

    (None) 

Reference Names:
================

    (None) 

Selected items not to be updated  (Same version as library)
===========================================================

Components:
===========

2WP (DSC)
BC547 (DSC)
BC556 (DSC)
BORNA_DOBLE (DIL)
BORNA_TRIPLE (DIL)
NUCLEOF446 (DIL)
R (DSC)

Symbols:
========

2-connector-board C:\Users\Public\Documents\DesignSpark PCB 9.0\Library\Default\DesignSpark.psl
BORNA_DOBLE       C:\Users\Public\Documents\DesignSpark PCB 9.0\Library\User\User.psl
BORNA_TRIPLE      C:\Users\Public\Documents\DesignSpark PCB 9.0\Library\User\User.psl
DISC04            C:\Users\Public\Documents\DesignSpark PCB 9.0\Library\Default\DesignSpark.psl
Nucleof446        C:\Users\Public\Documents\DesignSpark PCB 9.0\Library\User\User.psl
TO92A             C:\Users\Public\Documents\DesignSpark PCB 9.0\Library\Default\DesignSpark.psl

Reference Names:
================

CONN1
CONN3
CONN6
CONN8
CONN9
CONN10
CONN13
CONN15
CONN16
CONN17
CONN18
CONN19
CONN20
CONN21
CONN22
CONN23
CONN24
CONN25
CONN26
CONN27
CONN30
CONN31
CONN32
CONN33
PL3
PL4
PL6
PL7
PL8
Q1
Q2
Q3
Q4
Q5
Q6
Q7
Q8
Q9
Q10
R1
R2
R3
R4
R5
R6
R7
R8
R9
R10
R11
R12
R13
R14
R15
R16
R17
R18
R19
R20
R21
R22
R23
R24
R25
R26
R27
R28
R29
R30
U1

Update Components Summary
=========================

Updating components chosen from browser.
Update component values
Update component value positions
(Do not remove pad style exceptions on updated components)
	Selected for update:			   7  Components
						   6  Symbols
	Selected items to be updated:		   0  Components
						   0  Symbols
	Additional items to be updated:		   0  Components
						   0  Symbols
	Selected items NOT to be updated:	   7  Components
	  (Same version as library)		   6  Symbols

End Of Report.

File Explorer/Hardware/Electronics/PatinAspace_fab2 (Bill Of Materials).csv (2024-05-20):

Report Written: | Tuesday, June 21, 2022
Project Path: | C:\Users\ATC\Desktop\DISEÑO_PCB\DISEÑO_PCB\PatinAspace2\PatinAspace_fab.prj
Design Path: | C:\Users\ATC\Desktop\DISEÑO_PCB\DISEÑO_PCB\PatinAspace2\PatinAspace_fab2.pcb
Design Title:
Created: | 25/05/2021 8:12:04
Last Saved: | 10/06/2022 11:18:30
Editing Time: | 6773 min
Units: | mm (precision 2)
Bill of Materials generated with DesignSpark PCB - www.DesignSpark.com/pcb
--------------------------------------------------------------------------
Ref Name | Qty | Component | Value | Package | Manufacturer | MPN | RS Part Number | Other Part Number | Description
PL3 | 1 | 2WP |  | DSC |  |  |  |  | 2 way Pin Header
PL4 | 1 | 2WP |  | DSC |  |  |  |  | 2 way Pin Header
PL6 | 1 | 2WP |  | DSC |  |  |  |  | 2 way Pin Header
PL7 | 1 | 2WP |  | DSC |  |  |  |  | 2 way Pin Header
PL8 | 1 | 2WP |  | DSC |  |  |  |  | 2 way Pin Header
Q1 | 1 | BC547 |  | DSC |  |  |  |  | NPN Bipolar
Q2 | 1 | BC547 |  | DSC |  |  |  |  | NPN Bipolar
Q3 | 1 | BC547 |  | DSC |  |  |  |  | NPN Bipolar
Q4 | 1 | BC547 |  | DSC |  |  |  |  | NPN Bipolar
Q5 | 1 | BC547 |  | DSC |  |  |  |  | NPN Bipolar
Q6 | 1 | BC547 |  | DSC |  |  |  |  | NPN Bipolar
Q8 | 1 | BC547 |  | DSC |  |  |  |  | NPN Bipolar
Q9 | 1 | BC547 |  | DSC |  |  |  |  | NPN Bipolar
Q7 | 1 | BC556 |  | DSC |  |  |  |  | PNP Bipolar
Q10 | 1 | BC556 |  | DSC |  |  |  |  | PNP Bipolar
CONN1 | 1 | BORNA_DOBLE |  | DIL |  |  |  |  | BORNA_DOBLE
CONN6 | 1 | BORNA_DOBLE |  | DIL |  |  |  |  | BORNA_DOBLE
CONN13 | 1 | BORNA_DOBLE |  | DIL |  |  |  |  | BORNA_DOBLE
CONN15 | 1 | BORNA_DOBLE |  | DIL |  |  |  |  | BORNA_DOBLE
CONN16 | 1 | BORNA_DOBLE |  | DIL |  |  |  |  | BORNA_DOBLE
CONN18 | 1 | BORNA_DOBLE |  | DIL |  |  |  |  | BORNA_DOBLE
CONN20 | 1 | BORNA_DOBLE |  | DIL |  |  |  |  | BORNA_DOBLE
CONN21 | 1 | BORNA_DOBLE |  | DIL |  |  |  |  | BORNA_DOBLE
CONN22 | 1 | BORNA_DOBLE |  | DIL |  |  |  |  | BORNA_DOBLE
CONN23 | 1 | BORNA_DOBLE |  | DIL |  |  |  |  | BORNA_DOBLE
CONN24 | 1 | BORNA_DOBLE |  | DIL |  |  |  |  | BORNA_DOBLE
CONN32 | 1 | BORNA_DOBLE |  | DIL |  |  |  |  | BORNA_DOBLE
CONN33 | 1 | BORNA_DOBLE |  | DIL |  |  |  |  | BORNA_DOBLE
CONN34 | 1 | BORNA_DOBLE |  | DIL |  |  |  |  | BORNA_DOBLE
CONN8 | 1 | BORNA_TRIPLE |  | DIL |  |  |  |  | BORNA_TRIPLE
CONN9 | 1 | BORNA_TRIPLE |  | DIL |  |  |  |  | BORNA_TRIPLE
CONN10 | 1 | BORNA_TRIPLE |  | DIL |  |  |  |  | BORNA_TRIPLE
CONN19 | 1 | BORNA_TRIPLE |  | DIL |  |  |  |  | BORNA_TRIPLE
CONN25 | 1 | BORNA_TRIPLE |  | DIL |  |  |  |  | BORNA_TRIPLE
CONN26 | 1 | BORNA_TRIPLE |  | DIL |  |  |  |  | BORNA_TRIPLE
CONN27 | 1 | BORNA_TRIPLE |  | DIL |  |  |  |  | BORNA_TRIPLE
CONN30 | 1 | BORNA_TRIPLE |  | DIL |  |  |  |  | BORNA_TRIPLE
CONN31 | 1 | BORNA_TRIPLE |  | DIL |  |  |  |  | BORNA_TRIPLE
CONN11 | 1 | BORNA_TRIPLE |  | DIL |  |  |  |  | BORNA_TRIPLE
CONN28 | 1 | BORNA_TRIPLE |  | DIL |  |  |  |  | BORNA_TRIPLE
U1 | 1 | NUCLEOF446 |  | DIL
R1 | 1 | R | 1K | DSC |  |  |  |  | Resistor
R3 | 1 | R | 1K | DSC |  |  |  |  | Resistor
R6 | 1 | R | 1K | DSC |  |  |  |  | Resistor
R8 | 1 | R | 1K | DSC |  |  |  |  | Resistor
R9 | 1 | R | 1K | DSC |  |  |  |  | Resistor
R13 | 1 | R | 1k | DSC |  |  |  |  | Resistor
R14 | 1 | R | 1k | DSC |  |  |  |  | Resistor
R15 | 1 | R | 1k | DSC |  |  |  |  | Resistor
R16 | 1 | R | 1k | DSC |  |  |  |  | Resistor
R18 | 1 | R | 1k | DSC |  |  |  |  | Resistor
R21 | 1 | R | 1k | DSC |  |  |  |  | Resistor
R23 | 1 | R | 1K | DSC |  |  |  |  | Resistor
R25 | 1 | R | 1K | DSC |  |  |  |  | Resistor
R27 | 1 | R | 1k | DSC |  |  |  |  | Resistor
R28 | 1 | R | 1k | DSC |  |  |  |  | Resistor
R32 | 1 | R | 1K | DSC |  |  |  |  | Resistor
R2 | 1 | R | 3.3k | DSC |  |  |  |  | Resistor
R4 | 1 | R | 3.3k | DSC |  |  |  |  | Resistor
R5 | 1 | R | 3.3k | DSC |  |  |  |  | Resistor
R7 | 1 | R | 3.3k | DSC |  |  |  |  | Resistor
R10 | 1 | R | 3.3k | DSC |  |  |  |  | Resistor
R24 | 1 | R | 3.3k | DSC |  |  |  |  | Resistor
R26 | 1 | R | 3.3k | DSC |  |  |  |  | Resistor
R31 | 1 | R | 3.3k | DSC |  |  |  |  | Resistor
R17 | 1 | R | 10k | DSC |  |  |  |  | Resistor
R22 | 1 | R | 10k | DSC |  |  |  |  | Resistor
R29 | 1 | R | 220 | DSC |  |  |  |  | Resistor
R30 | 1 | R | 220 | DSC |  |  |  |  | Resistor
R11 | 1 | R | 272 | DSC |  |  |  |  | Resistor
R12 | 1 | R | 272 | DSC |  |  |  |  | Resistor
R19 | 1 | R | 272 | DSC |  |  |  |  | Resistor
R20 | 1 | R | 272 | DSC |  |  |  |  | Resistor

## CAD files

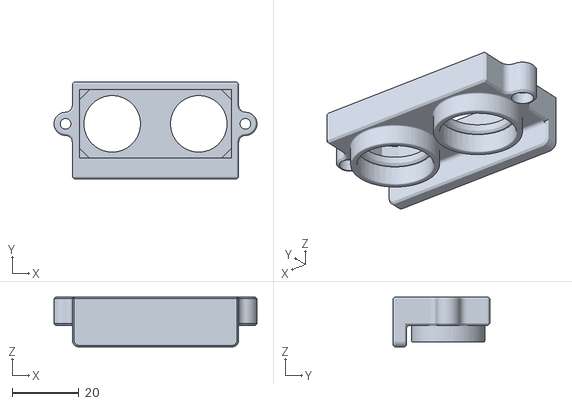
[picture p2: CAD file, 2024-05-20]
Explorer/Hardware/Mechanics/Soporte ultrasonido 2.STL
61.0 x 29.0 x 15.0

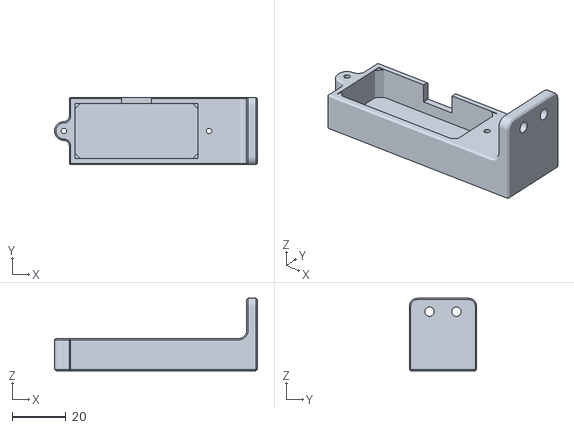
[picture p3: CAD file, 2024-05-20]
Explorer/Hardware/Mechanics/Soporte ultrasonido 1.6.STL
75.5 x 25.0 x 27.0

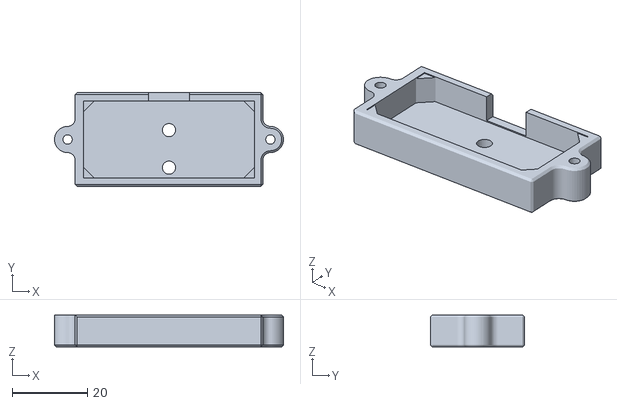
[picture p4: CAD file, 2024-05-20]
Explorer/Hardware/Mechanics/Soporte ultrasonido 1.2.STL
61.0 x 25.0 x 8.50

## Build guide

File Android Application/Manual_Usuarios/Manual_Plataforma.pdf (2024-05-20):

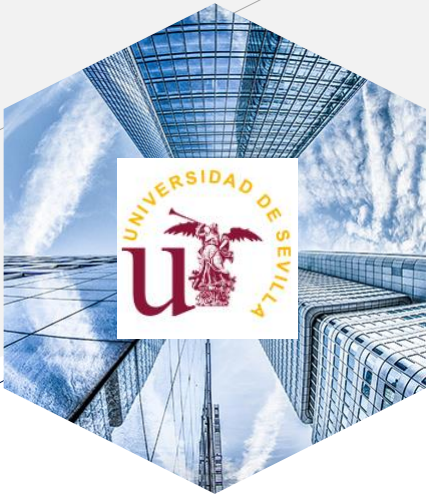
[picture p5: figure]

## Uso de la plataforma y de la aplicación

bluetooth.

M a n u a l d e l s i s t e m a y d e s c r i p c i ó n b á s i c a .

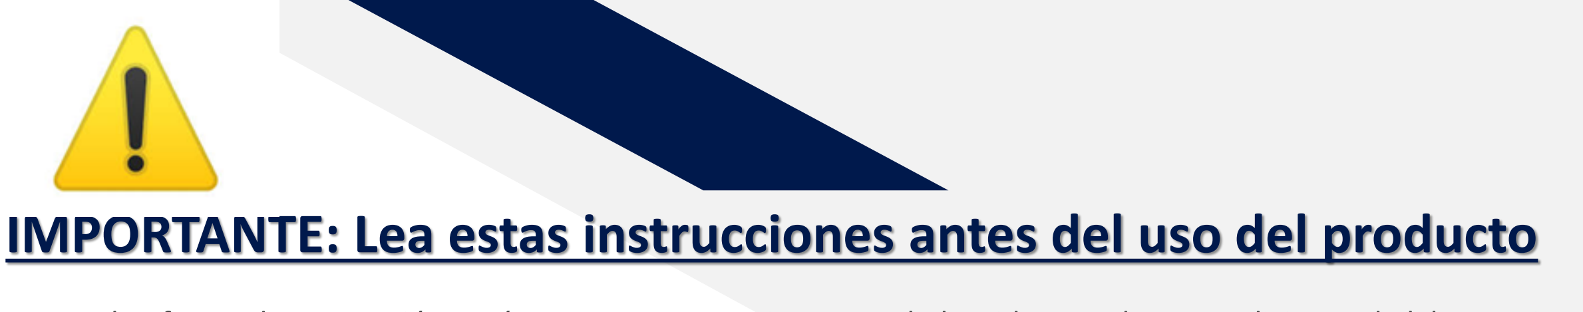
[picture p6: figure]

### IMPORTANTE: Lea estas instrucciones antes del uso del producto

- La plataforma de navegación autónoma es un prototipo que solo ha sido testada en condiciones de laboratorio y que, por tanto, carece de certificación industrial.
- Es obligatoria una supervisión permanente y continua de la misma por la persona responsable de su operación.
- Se recomienda su uso en espacios interiores amplios con poco mobiliario.
- Su uso no está permitido en exteriores, y, en general, en lugares con rampas de acceso o presenten diferentes niveles del suelo (escenarios, cerca de escalones o escaleras, etc.)
- La plataforma incorpora sensores para la detección de obstáculos que se encuentren cerca de la superficie del suelo. Se deberá tener especial cuidado cuando ésta se acerque a elementos con estructuras salientes (mesas, extintores, etc.) que puedan golpear al infante.
- El cordel de seguridad debe estar colocado en todo momento. En caso de necesidad, tire de él para interrumpir la alimentación de la plataforma y forzar su parada.
- En todo momento deberá tener conectado el móvil con la plataforma, pudiéndole ordenar su parada si fuera necesario.
- Tenga en cuenta que cualquier parada de emergencia no es inmediata, pues el conjunto presenta una inercia.
- La responsabilidad de los daños que ésta pueda originar recaerá siempre en la persona a cargo de la supervisión de la misma durante su uso.

# Características del sistema

Este dispositivo es un prototipo cuyo fin es la navegación autónoma de una silla de ruedas acoplada a una plataforma móvil. Es necesaria la aplicación (App) que hace de interfaz entre la plataforma y el usuario.
Dicho software es imprescindible para el funcionamiento de la plataforma. Mediante la App, la persona a cargo de la plataforma, podrá establecer, primero, conexión con la misma, lo que habilita su funcionamiento, y después, configurar su velocidad y tiempo de funcionamiento. También se podrá llevar a cabo la gestión del paro e inicio de la sesión.

# 1. Descripción general y uso de la plataforma

## Colocación de silla en plataforma

Para colocar adecuadamente la silla del usuario en la plataforma hay que proceder de una manera específica.
En primer lugar, alinear la silla con la plataforma, siempre con el eje trasero bajado:
- Eje basculante para acoplar la silla a la plataforma.

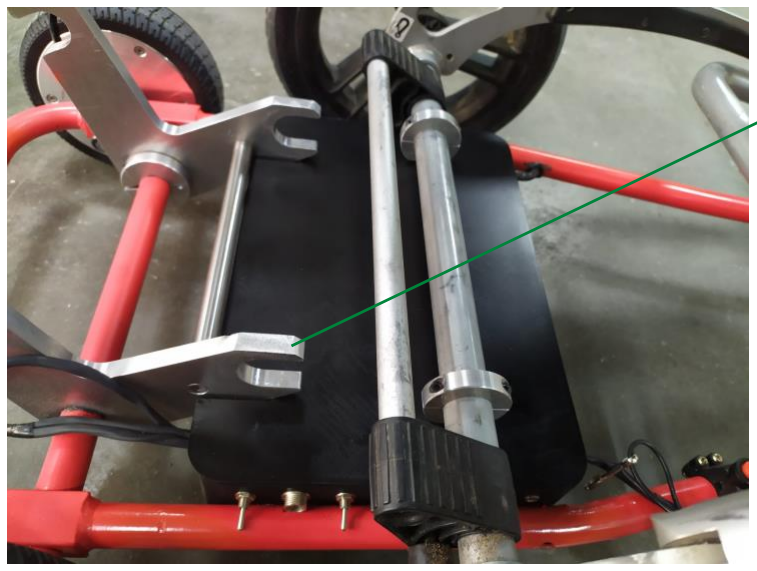
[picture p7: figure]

## Colocación de silla en plataforma

Alinear la silla con la plataforma para que las cogidas del eje queden acopladas en la parte interior de los topes:

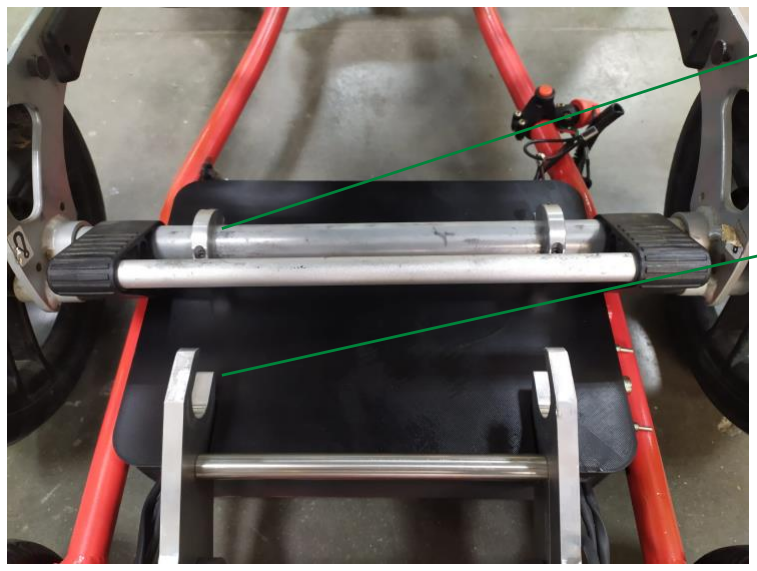
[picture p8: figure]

- Eje alineado con los topes laterales de la silla.
- Topes laterales agregados a la silla.

## Colocación de silla en plataforma

Acoplar silla y plataforma como indican las siguientes figuras:

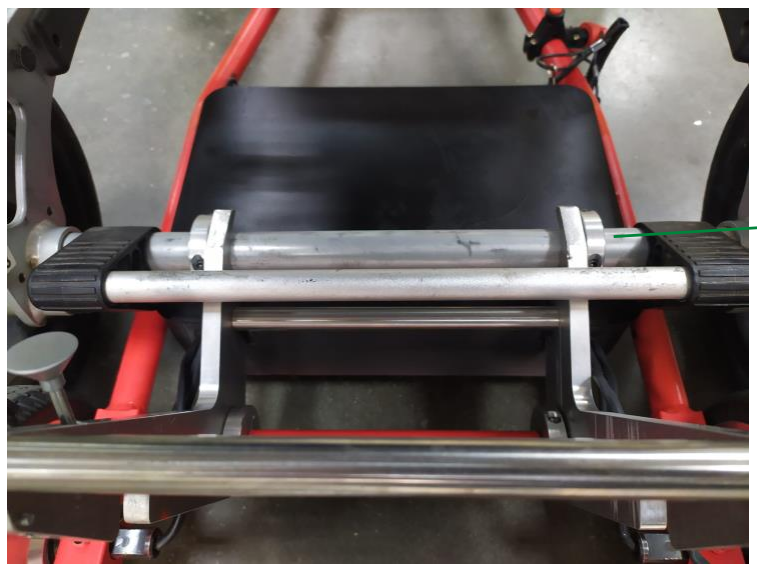
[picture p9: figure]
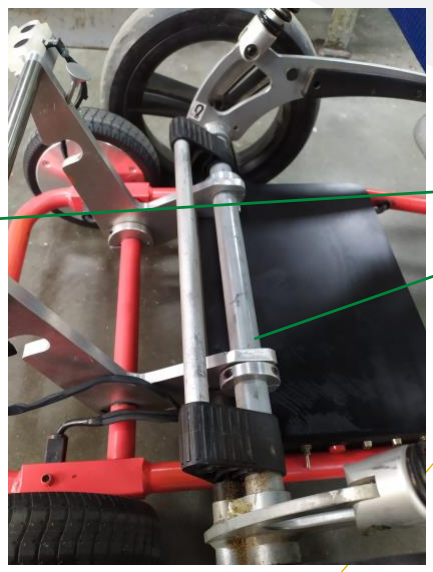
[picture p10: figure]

- Forma correcta del
acoplamiento.

## Colocación de silla en plataforma

Tras el acople, procedemos a empujar en dirección al suelo la barra que hace bascular el eje hasta dejar las ruedas traseras de la silla en el aire y las muescas encajadas en la plataforma.

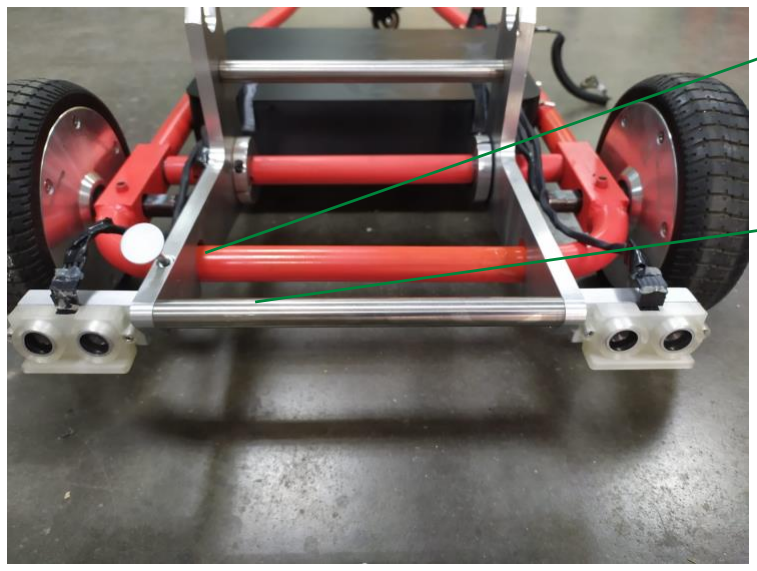
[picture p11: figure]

- Barra que bascula el eje.
- Muescas que han de
encajar en la plataforma.

## Colocación de silla en plataforma

Por último, es imprescindible enclavar la silla con la plataforma mediante un resorte de seguridad que cerraremos.
- Resorte de seguridad
abierto.

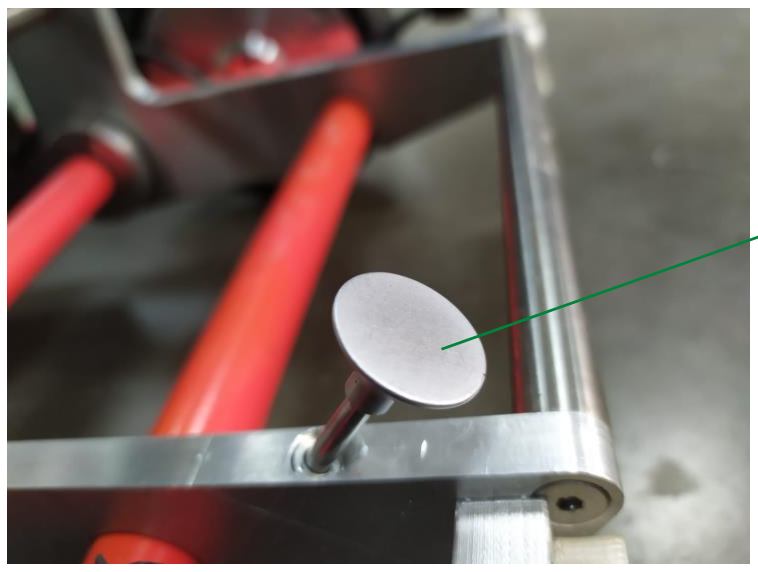
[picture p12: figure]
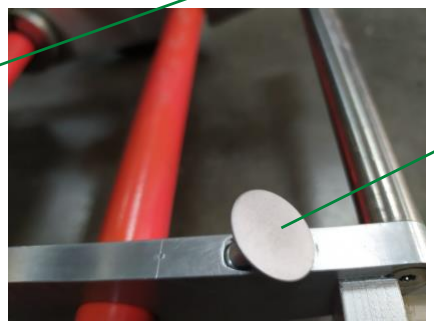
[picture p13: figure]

- Resorte de seguridad
cerrado.

La plataforma dispone de una centralita de control donde se gestiona el conjunto del sistema. Por su condición de prototipo, dispone de elementos en el frontal que solo son para el testeo y puesta en macha de éste y que no se deben manipular. Se muestra a continuación cuales son:

# Uso de la plataforma

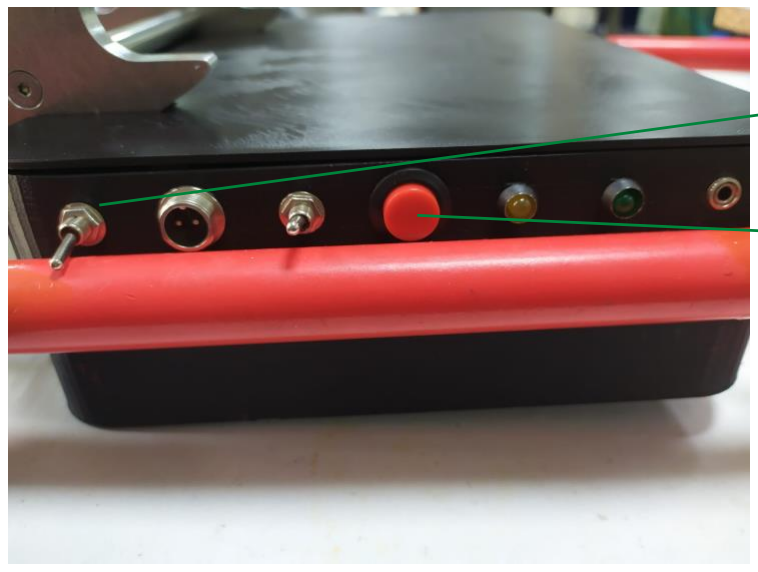
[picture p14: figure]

- Interruptor de
programación.
- Botón de tester.

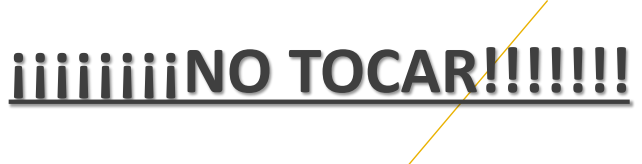
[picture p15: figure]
¡¡¡¡¡¡¡¡NO TOCAR!!!!!!!

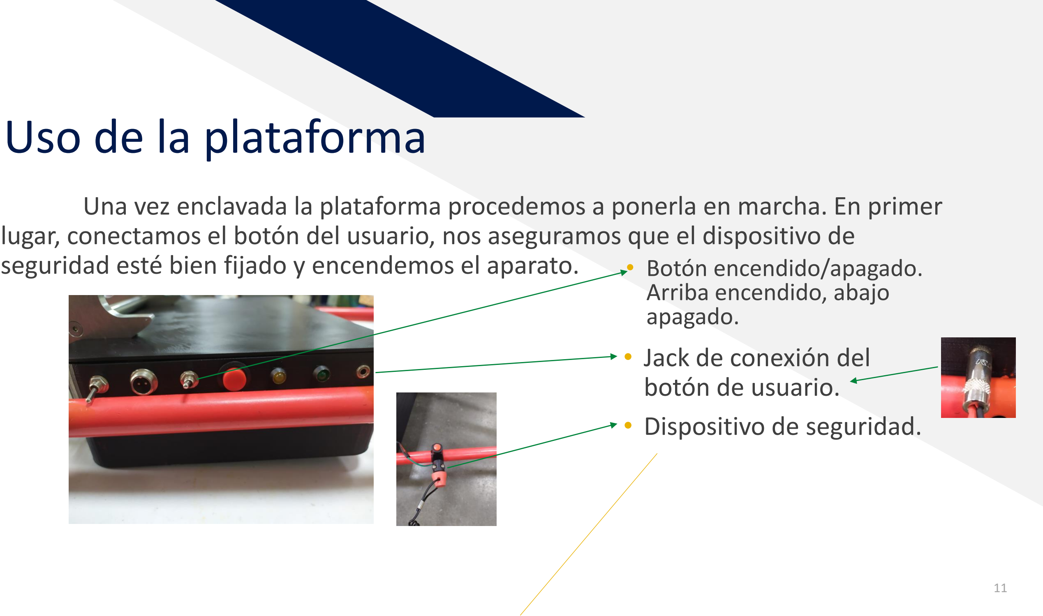
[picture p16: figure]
Uso de la plataforma; • Jack de conexión del botón de usuario. • Dispositivo de seguridad.; • Botón encendido/apagado. Arriba encendido, abajo apagado.

Una vez enclavada la plataforma procedemos a ponerla en marcha. En primer lugar, conectamos el botón del usuario, nos aseguramos que el dispositivo de seguridad esté bien fijado y encendemos el aparato.

# Uso de la plataforma

El dispositivo de seguridad garantiza la desconexión eléctrica total de la plataforma en caso de percance o comportamiento anómalo solo tirando del cordel. La capucha encajada se soltará desconectando la electricidad. Para restablecer el sistema hay que colocarla tal y como estaba antes de la incidencia.
- Capucha adosada al
dispositivo de seguridad.
- Cordel de seguridad.

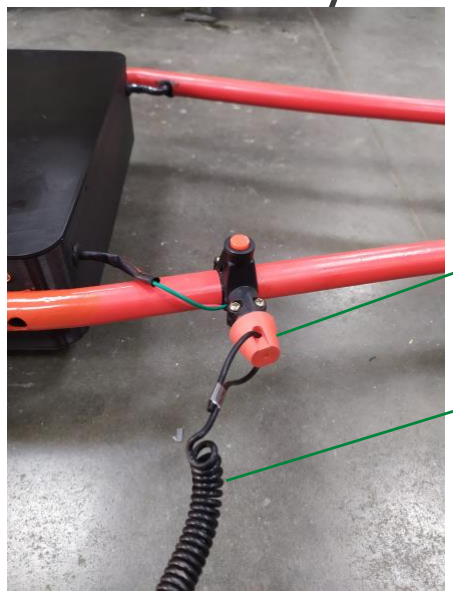
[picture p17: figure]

# Uso de la plataforma

Teniendo encendida la plataforma, que se indicará mediante un led, se debe iniciar la aplicación del móvil para poder comenzar a usarla.

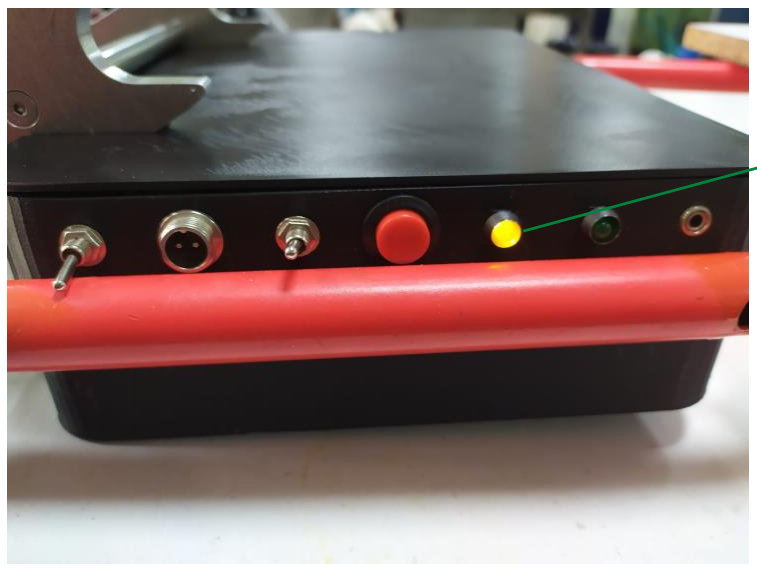
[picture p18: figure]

- Led que indica que la
plataforma está alimentada eléctricamente.

# Carga de la plataforma

Apagaremos la plataforma mediante el botón de encendido/apagado, y conectaremos el cargador a la misma.
- Led que indica que la
plataforma está apagada o
encendida.
- Botón hacia abajo en
posición de apagado.
- Conector de carga de la
plataforma.

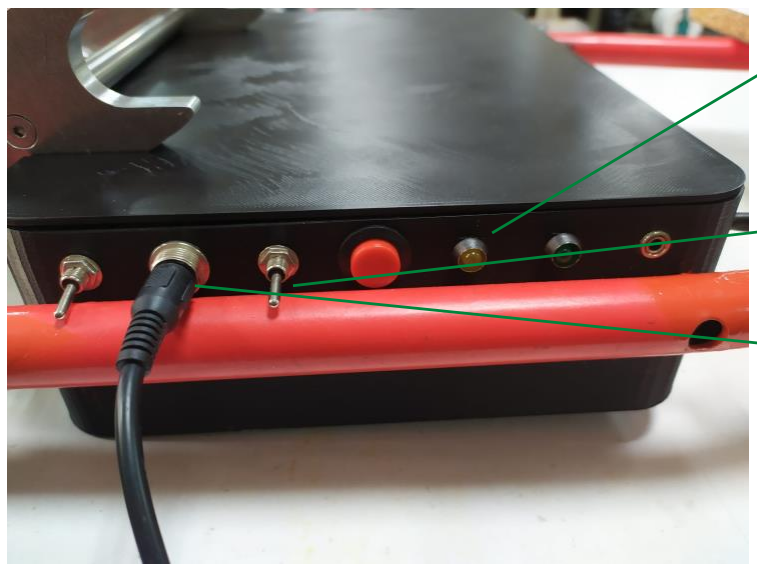
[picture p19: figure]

# Carga de la plataforma

El alimentador de carga mediante un led indicador mostrará si se está cargando o cuando está totalmente cargado.

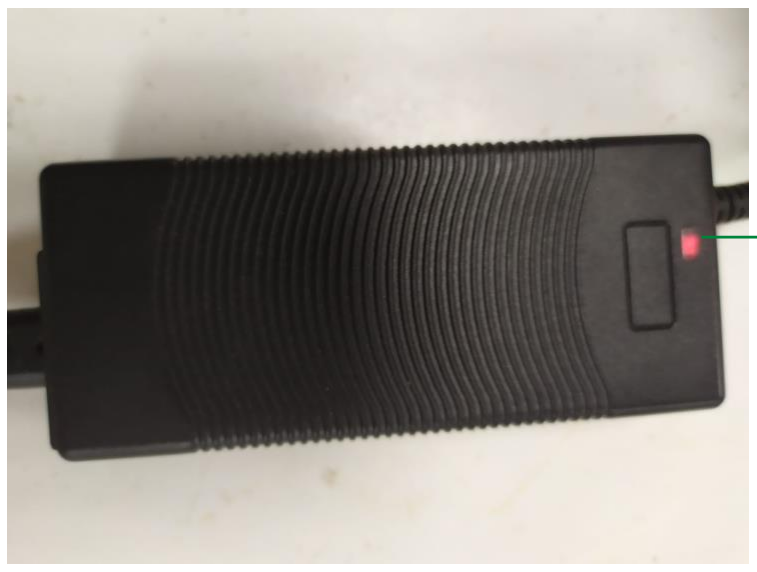
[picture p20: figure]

- Led rojo que indica que la plataforma se está cargando. Cuando pase a color verde
significa que la batería está totalmente cargada.

# 2. Descripción general de la Aplicación para Android

## Interfaz general y uso de la

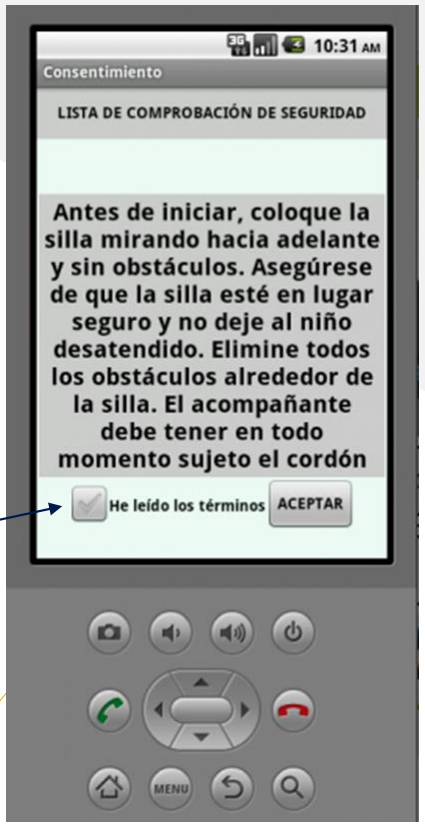
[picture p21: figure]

aplicación.

- Leer y cumplir
estrictamente la lista de
comprobación de seguridad
antes aceptar los términos.
- La primera vez que intentemos conecta

r
debemos vincular nuestro teléfono móvil con la plataforma, para ello en los ajustes del sistemas buscaremos el dispositivo llamado “Plataforma” y nos emparejaremos con él. Como medida de seguridad introduciremos la contraseña “1234”

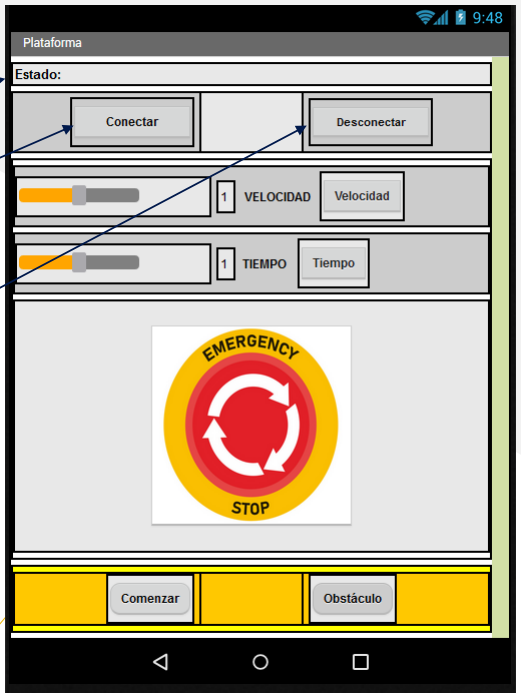
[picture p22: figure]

## Interfaz general y uso de la

aplicación.

- Con el botón de Conectar buscaremos dispositivos bluetooth para poder establecer la conexión con la plataforma. Debe listarse con el nombre “plataforma”
- Se podrá desemparejar el equipo hardware de la aplicación mediante
el botón Desconectar
- El indicador de Estado nos mostrará en la situación que se encuentra la conexión, pudiendo ser: Escaneando, Conectado o Desconectado.

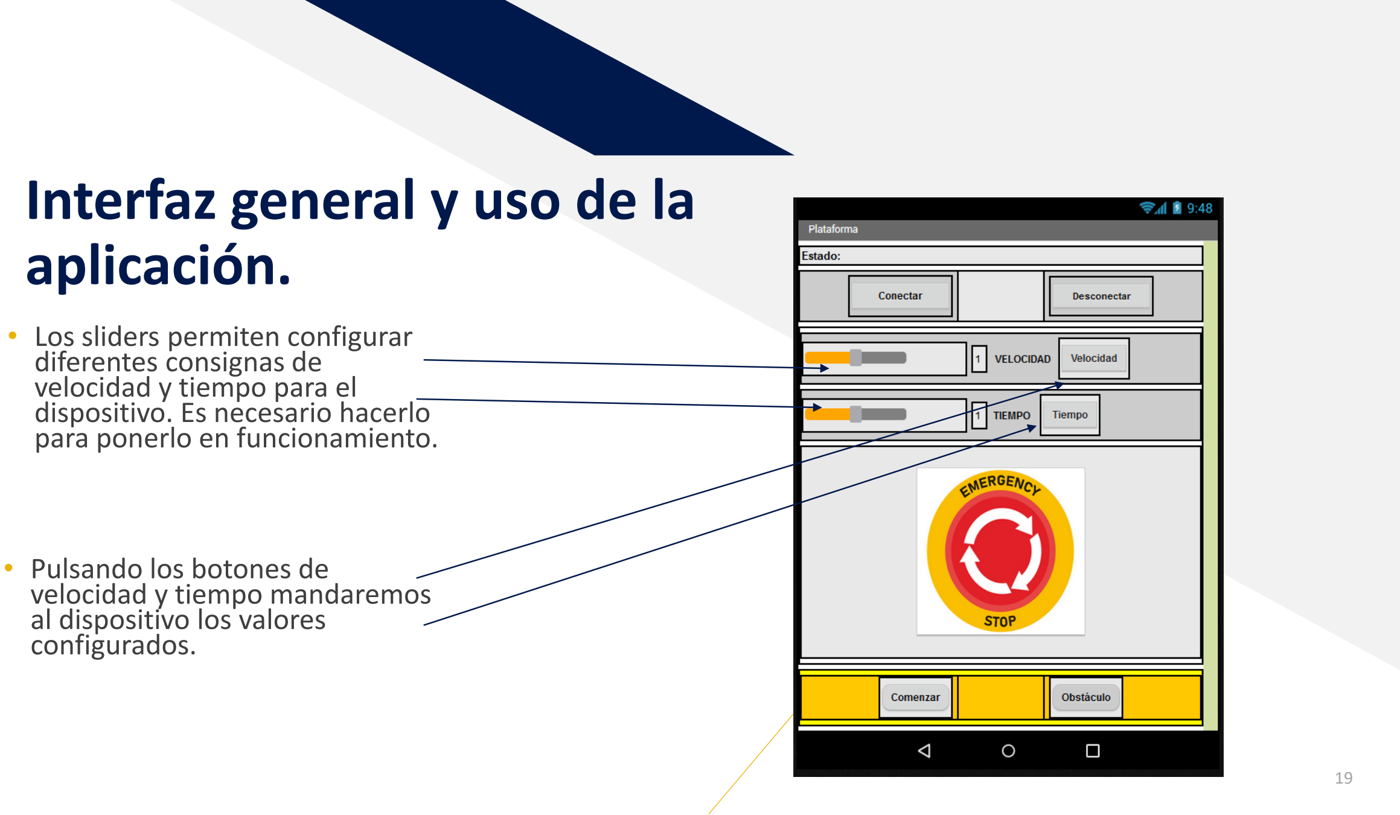
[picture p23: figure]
Interfaz general y uso de la aplicación.; • Los sliders permiten configurar diferentes consignas de velocidad y tiempo para el dispositivo. Es necesario hacerlo para ponerlo en funcionamiento.; • Pulsando los botones de velocidad y tiempo mandaremos al dispositivo los valores configurados.

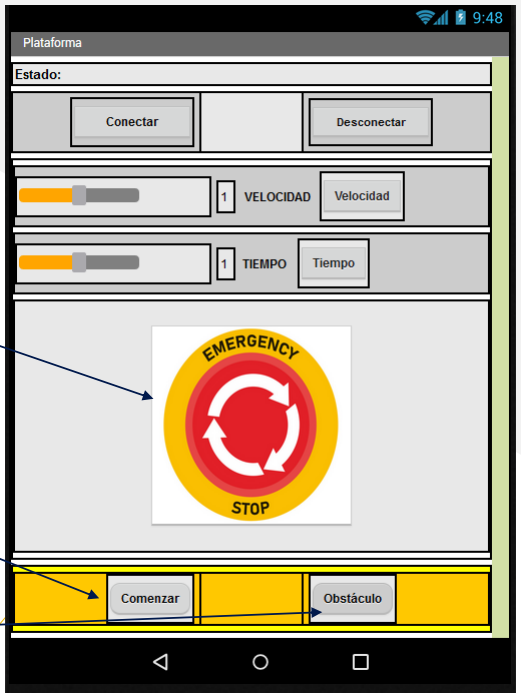
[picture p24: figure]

## Interfaz general y uso de la

aplicación.

- El botón Comenzar permite comenzar la secuencia de funcionamiento con la velocidad y tiempo configurado. Es imprescindible para que la plataforma inicie el movimiento pulsar el botón de usuario.
- Con el botón Obstáculo podremos simular la detección de obstáculos generando movimientos pseudo aleatorios en la plataforma.
- El pulsador de paro manda un comando que para
inmediatamente ambos motores.

# 3. Resumen y pasos para el

funcionamiento.

# Resumen puesta en marcha

1. Alineamos la plataforma con la silla y montamos en ella.
2. Conectamos el Jack de usuario y nos aseguramos que la capucha de seguridad esté bien puesta.
3. Encendemos el dispositivo y el led debe encenderse, si no asegurarse que la capucha esté bien sujeta y que la batería esté cargada.
4. Arrancamos la aplicación del móvil.
5. Conectamos con la plataforma, le pasamos parámetros de velocidad y tiempo y pulsamos el botón de Comenzar.
6. Para que se inicie el movimiento es imprescindible pulsar el botón de usuario.
7. Cuando acabe el tiempo de movimiento debemos pulsar otra vez el botón de usuario.

# Resolución de fallos

1. Al encender la plataforma no se enciende ningún led.
- Asegurar que la capucha de seguridad está bien adosada al dispositivo de seguridad.
2. Error “unable to write broken pipe” en la aplicación del móvil cuando intentamos mandar algún comando. -Desconectar y volver a conectar la plataforma a la aplicación móvil.
3. La plataforma no se mueve aunque hayamos pulsado el botón de iniciar en la aplicación del móvil. -Cerciorarse siempre de pulsar el botón de usuario además del botón de iniciar de la aplicación.
4. La plataforma apenas cambia de velocidad al pasarle nuevos parámetros.
- Por cuestiones de seguridad, la velocidad es modificable dentro de unos parámetros muy bajos prácticamente inapreciables.
5. Comportamiento errático de la plataforma u observación de anomalías en la misma.
- Avisar a desarrolladores de la plataforma.

# Buen uso de la plataforma

Se recomienda encarecidamente debido a su naturaleza de prototipo tener una serie de precauciones básicas:

1. El sistema está basado en sensores de ultrasonidos, los cuales son extremadamente delicados a los golpes y tirones. Si se hace un uso indebido o no se tiene la delicadeza adecuada a la hora de almacenar o transportar la plataforma es probable que dichos sensores acaben sufriendo golpes que dejarían la plataforma sin utilidad además de provocar un comportamiento errático de la misma.
2. Es imprescindible mantener unos niveles de carga de la batería adecuados, si no es así también se pueden observar comportamientos anómalos en el sistema.
3. A la hora de desacoplar la silla de la plataforma, hay que asegurarse que el Jack del botón de usuario esté desconectado, en caso contrario recibirá un tirón que acabará destruyendo el conector.
4.Hay que tener en cuenta que la caja que controla la plataforma no es de fabricación industrial, si no un prototipo. Por lo tanto la brusquedad en el transporte o almacenaje puede provocar desconexiones interiores que generen la inutilización del prototipo.

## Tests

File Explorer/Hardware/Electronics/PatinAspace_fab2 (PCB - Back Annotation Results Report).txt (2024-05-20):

Back Annotation Results Report
------------------------------

Report Written:     Thursday, June 23, 2022
Project Path:       C:\Users\ATC\Desktop\DISEÑO_PCB\DISEÑO_PCB\PatinAspace2\PatinAspace_fab.prj
Design Path:        C:\Users\ATC\Desktop\DISEÑO_PCB\DISEÑO_PCB\PatinAspace2\PatinAspace_fab2.pcb
Design Title:       
Created:            25/05/2021 8:12:04
Last Saved:         23/06/2022 11:40:32
Editing Time:       6887 min
Units:              mm (precision 2)

Back Annotate renames from the PCB design to all Schematic designs in project "PatinAspace_fab".

Renamed Net from "enaRight" to "enaLeft1" in design "PatinAspace_fab2.sch".
Renamed Net from "enaRight" to "enaLeft1" in design "PatinAspace_fab2.sch".
Renamed Net from "enaLeft" to "enaRight" in design "PatinAspace_fab2.sch".
Renamed Net from "enaLeft" to "enaRight" in design "PatinAspace_fab2.sch".
Renamed Net from "enaLeft1" to "enaLeft" in design "PatinAspace_fab2.sch".
Renamed Net from "enaLeft1" to "enaLeft" in design "PatinAspace_fab2.sch".

End Of Report.

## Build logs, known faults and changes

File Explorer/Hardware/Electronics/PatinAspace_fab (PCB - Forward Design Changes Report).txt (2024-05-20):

Forward Design Changes Report
-----------------------------

Report Written:     Thursday, June 10, 2021
Project Path:       C:\Users\ATC\Desktop\DISEÑO_PCB\DISEÑO_PCB\PatinAspace\PatinAspace_fab.prj
Design Path:        C:\Users\ATC\Desktop\DISEÑO_PCB\DISEÑO_PCB\PatinAspace\PatinAspace_fab.pcb
Design Title:       
Created:            25/05/2021 8:12:04
Last Saved:         10/06/2021 9:41:58
Editing Time:       5001 min
Units:              mm (precision 2)

Net Echo2_Tim4Ch1 renamed to Echo2_Tim4Ch2
Net Echo3_Tim4Ch1 renamed to Echo3_Tim4Ch3
Net Echo5_Tim8Ch1 renamed to Echo5_Tim8Ch2

End Of Report.

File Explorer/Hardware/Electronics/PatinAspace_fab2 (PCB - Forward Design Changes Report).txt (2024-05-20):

Forward Design Changes Report
-----------------------------

Report Written:     Thursday, June 23, 2022
Project Path:       C:\Users\ATC\Desktop\DISEÑO_PCB\DISEÑO_PCB\PatinAspace2\PatinAspace_fab.prj
Design Path:        C:\Users\ATC\Desktop\DISEÑO_PCB\DISEÑO_PCB\PatinAspace2\PatinAspace_fab2.pcb
Design Title:       
Created:            25/05/2021 8:12:04
Last Saved:         23/06/2022 11:47:56
Editing Time:       6896 min
Units:              mm (precision 2)

Changed value "Value" on component reference "R27" to "4k7".
Changed value "Value" on component reference "R28" to "4k7".

End Of Report.

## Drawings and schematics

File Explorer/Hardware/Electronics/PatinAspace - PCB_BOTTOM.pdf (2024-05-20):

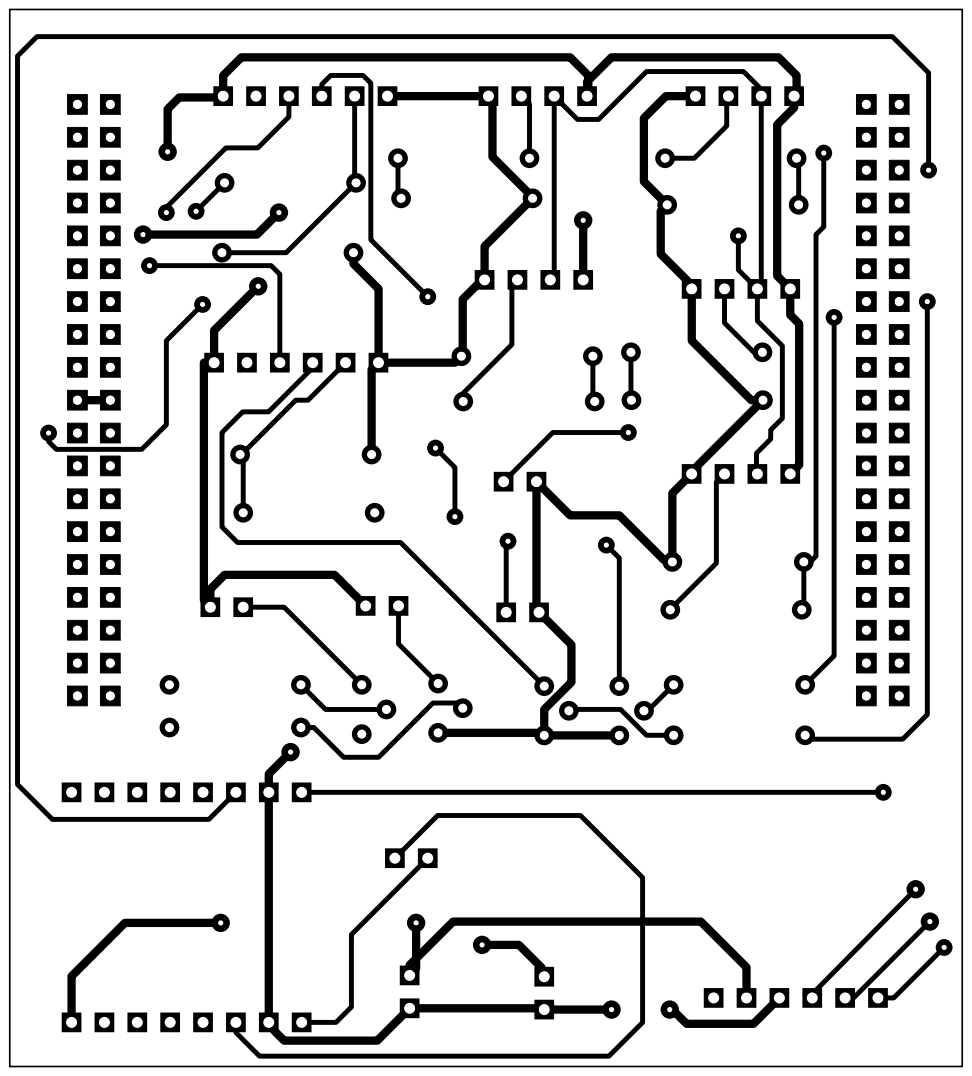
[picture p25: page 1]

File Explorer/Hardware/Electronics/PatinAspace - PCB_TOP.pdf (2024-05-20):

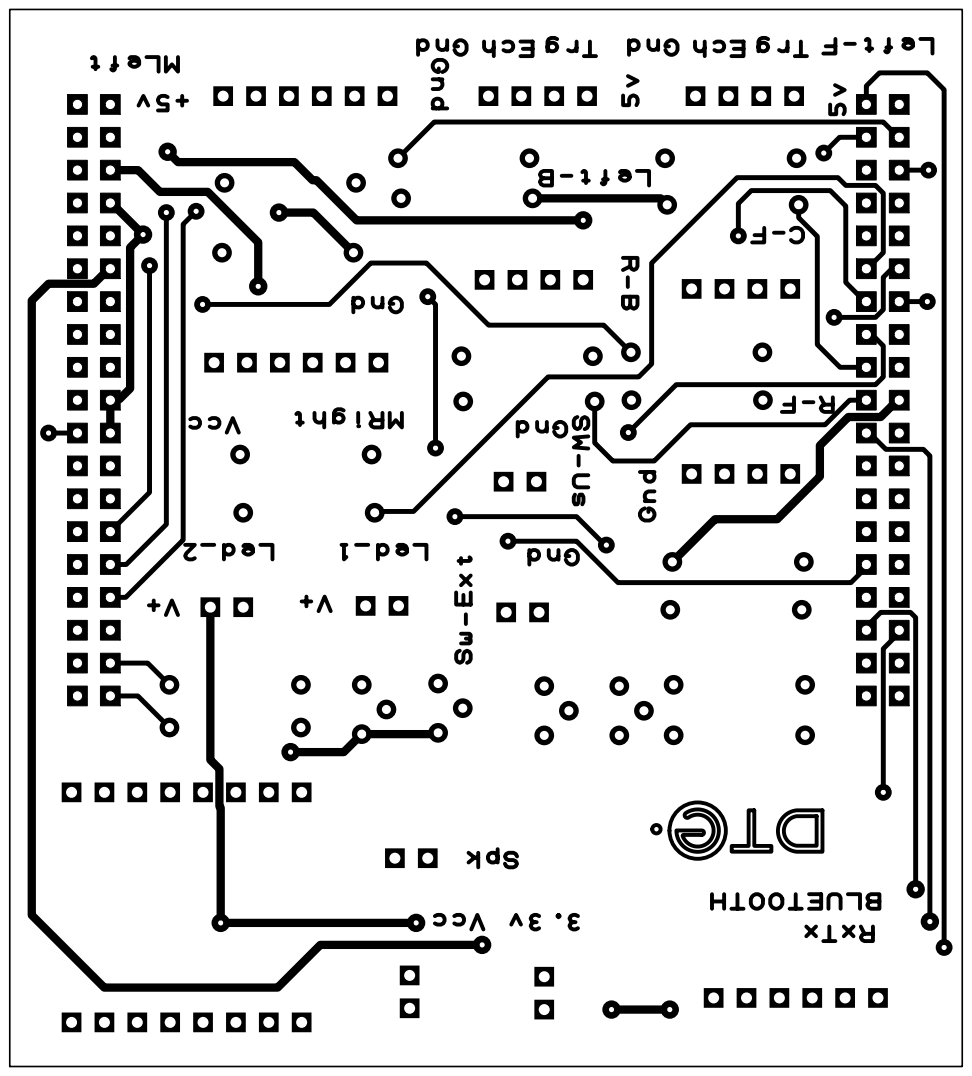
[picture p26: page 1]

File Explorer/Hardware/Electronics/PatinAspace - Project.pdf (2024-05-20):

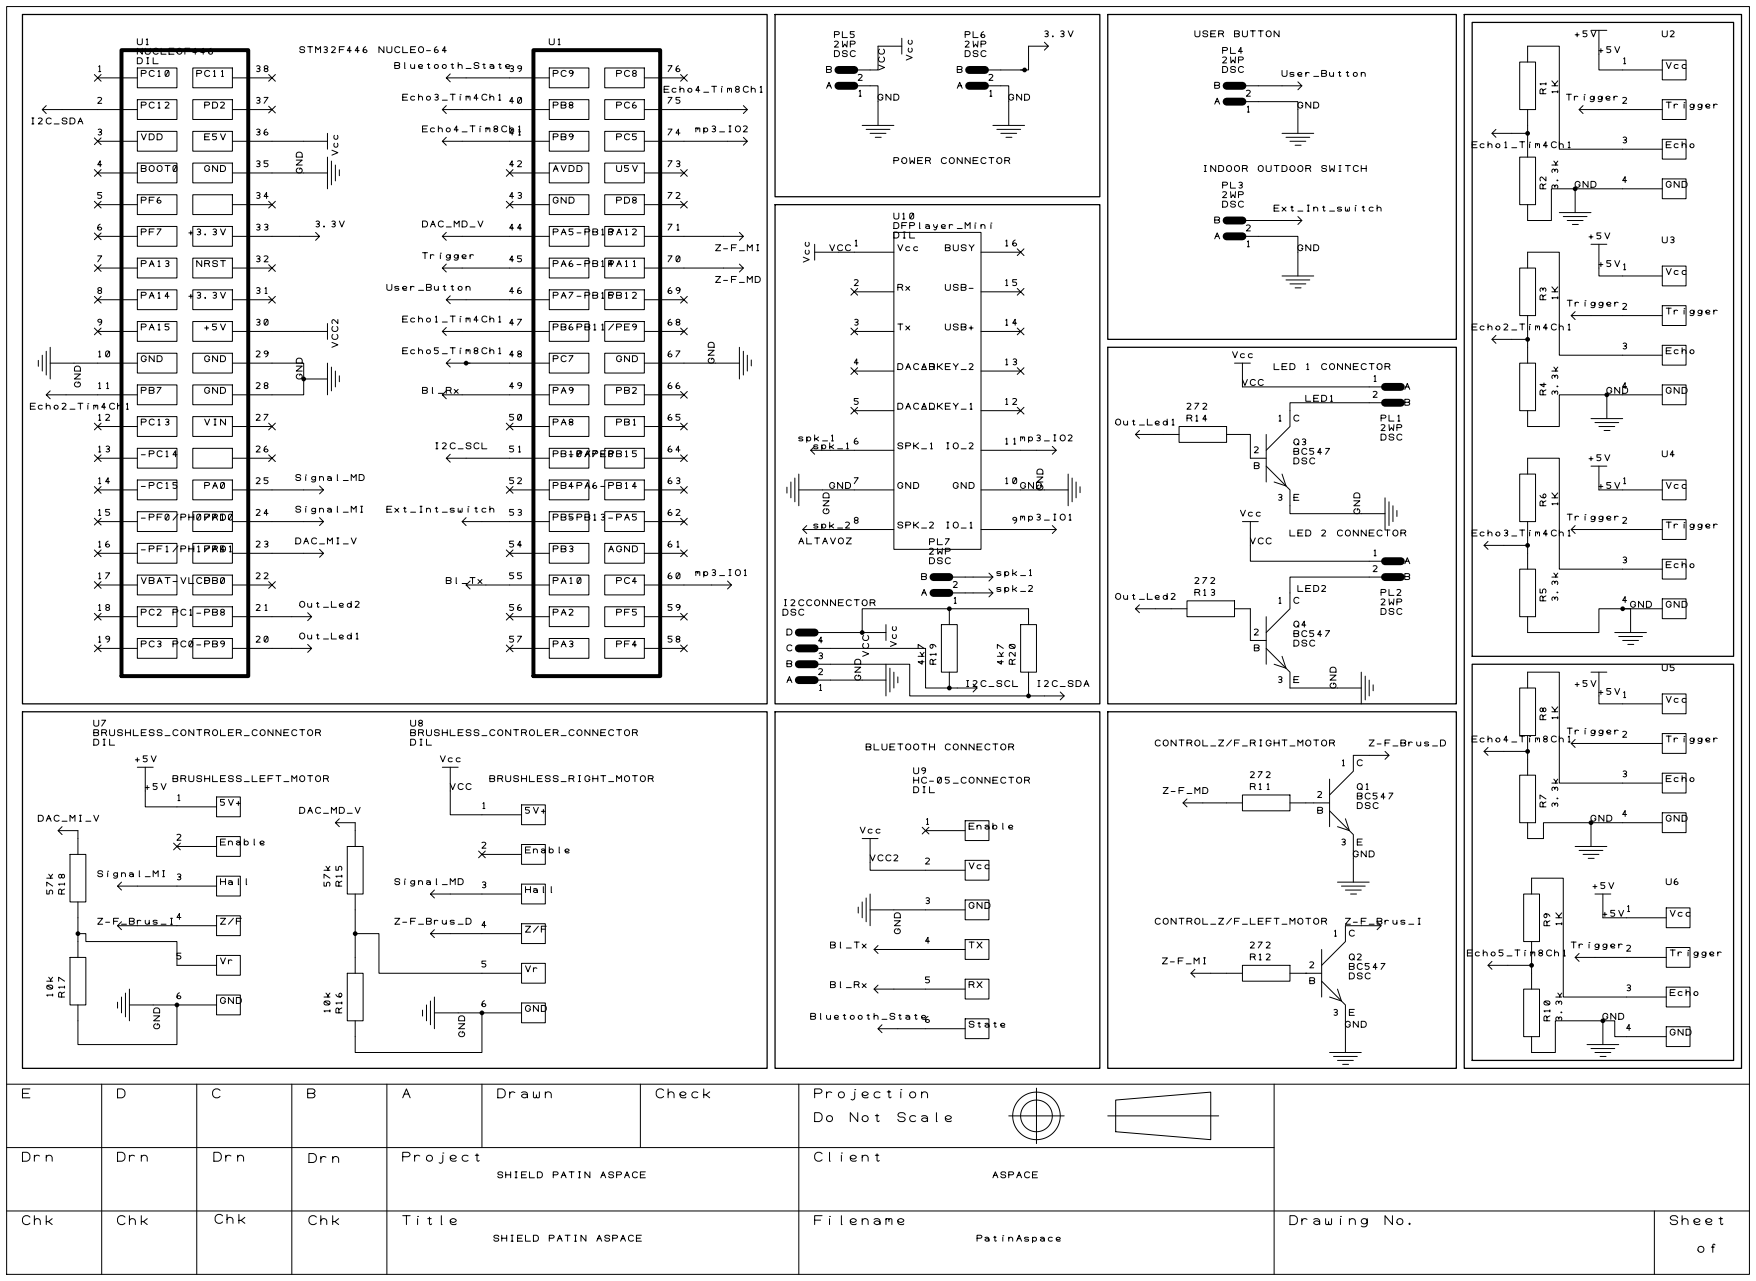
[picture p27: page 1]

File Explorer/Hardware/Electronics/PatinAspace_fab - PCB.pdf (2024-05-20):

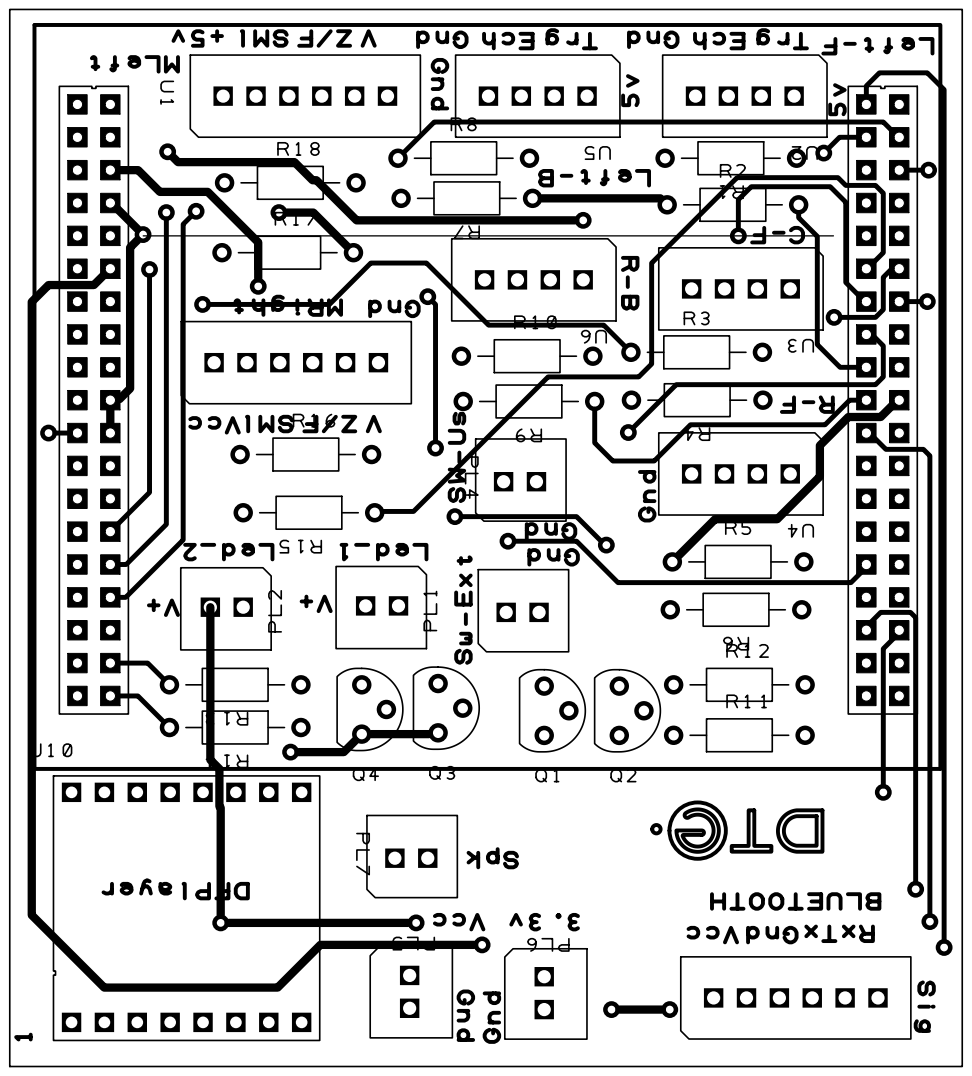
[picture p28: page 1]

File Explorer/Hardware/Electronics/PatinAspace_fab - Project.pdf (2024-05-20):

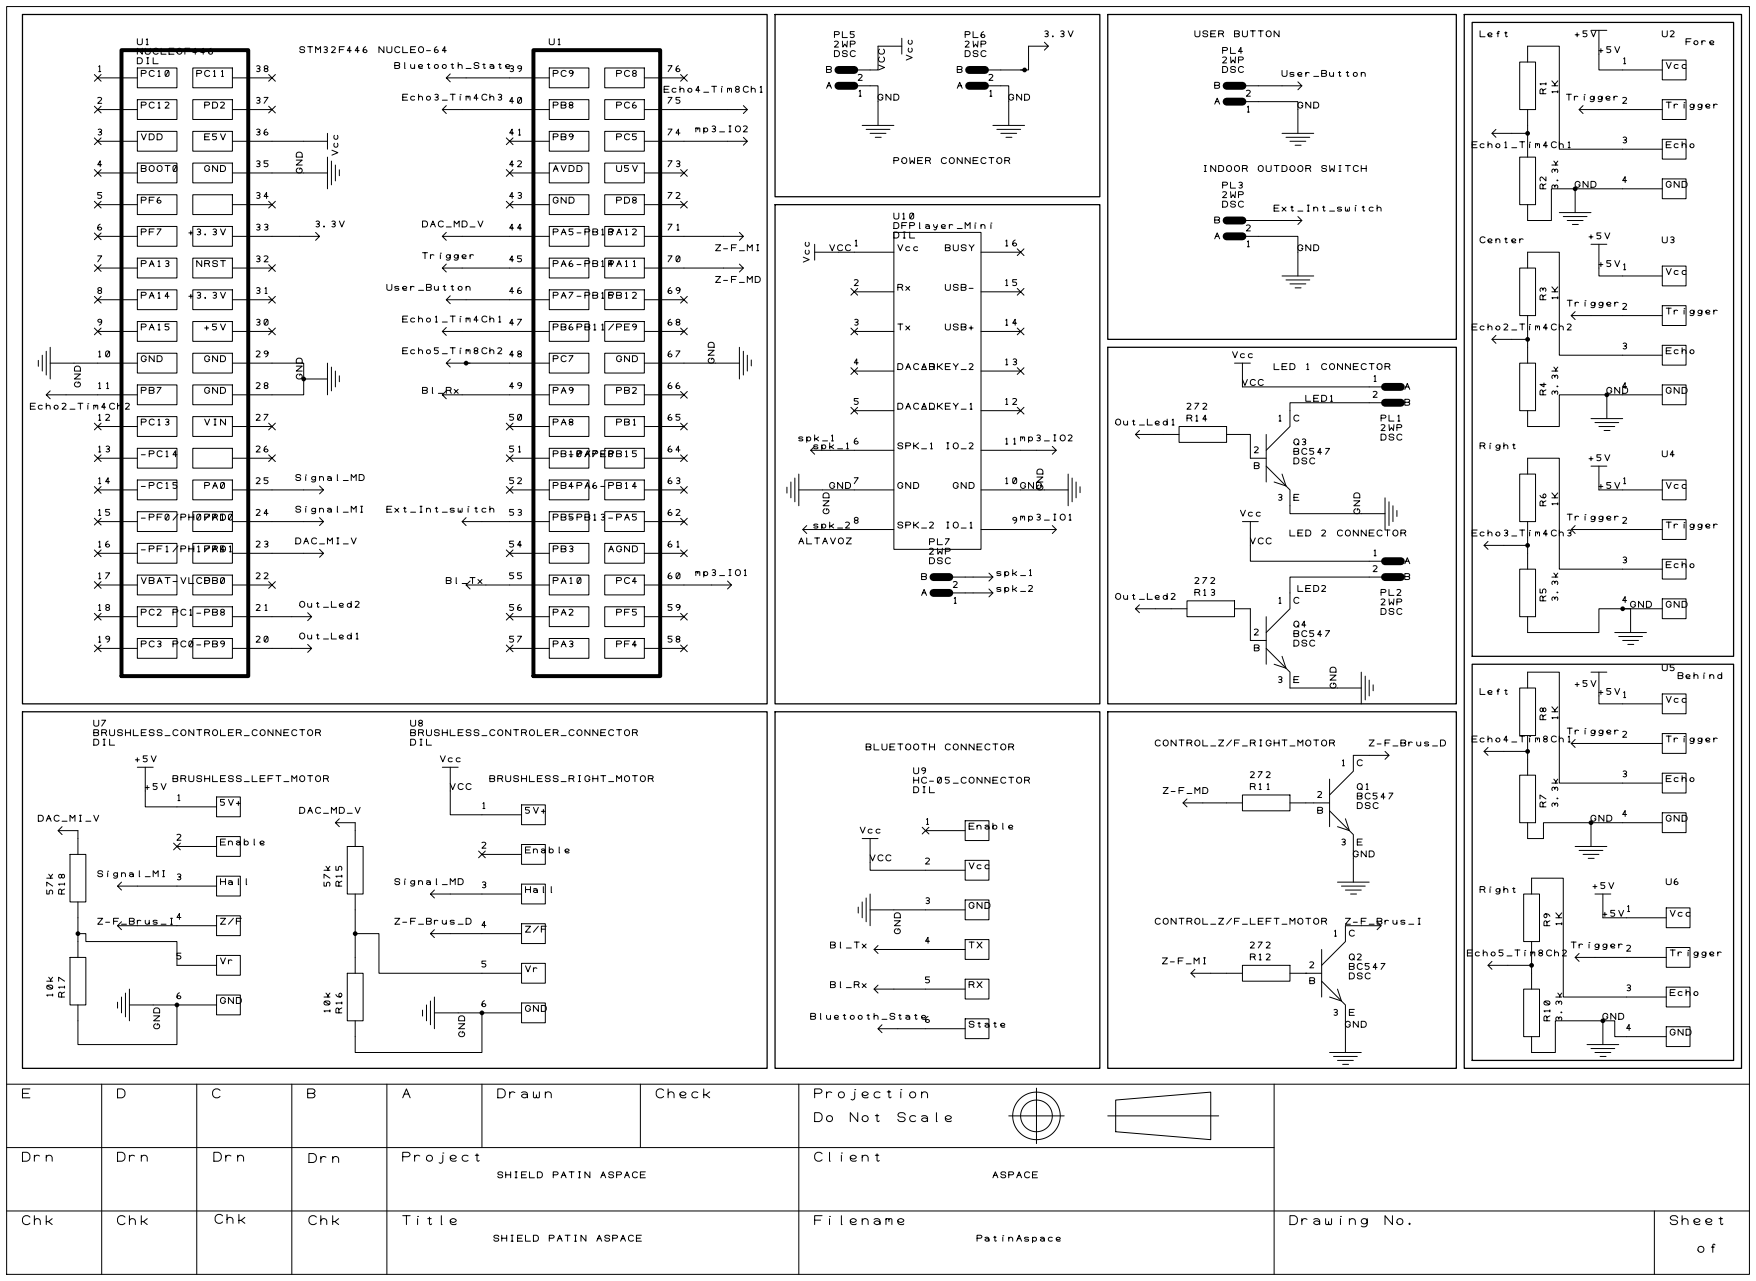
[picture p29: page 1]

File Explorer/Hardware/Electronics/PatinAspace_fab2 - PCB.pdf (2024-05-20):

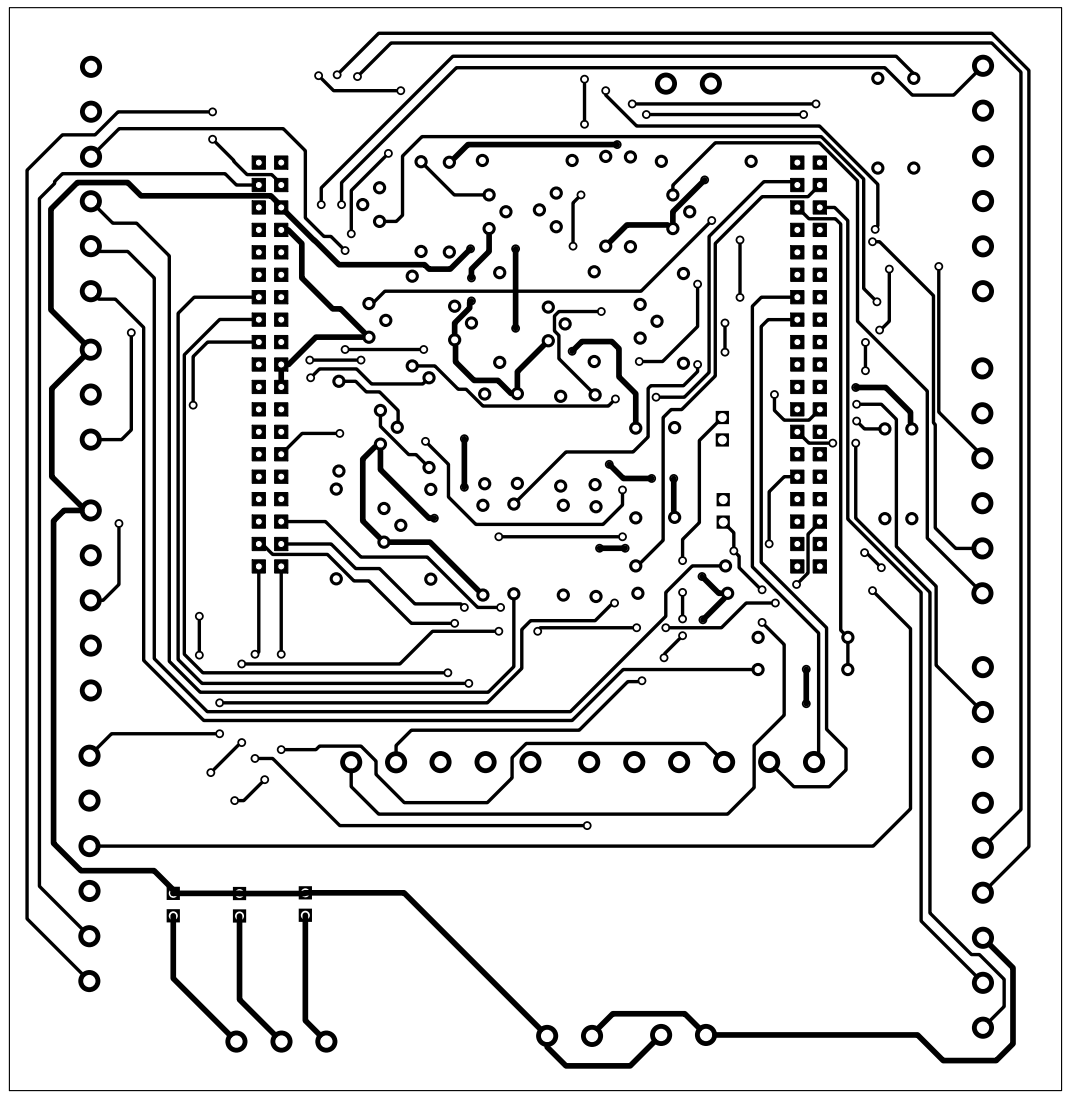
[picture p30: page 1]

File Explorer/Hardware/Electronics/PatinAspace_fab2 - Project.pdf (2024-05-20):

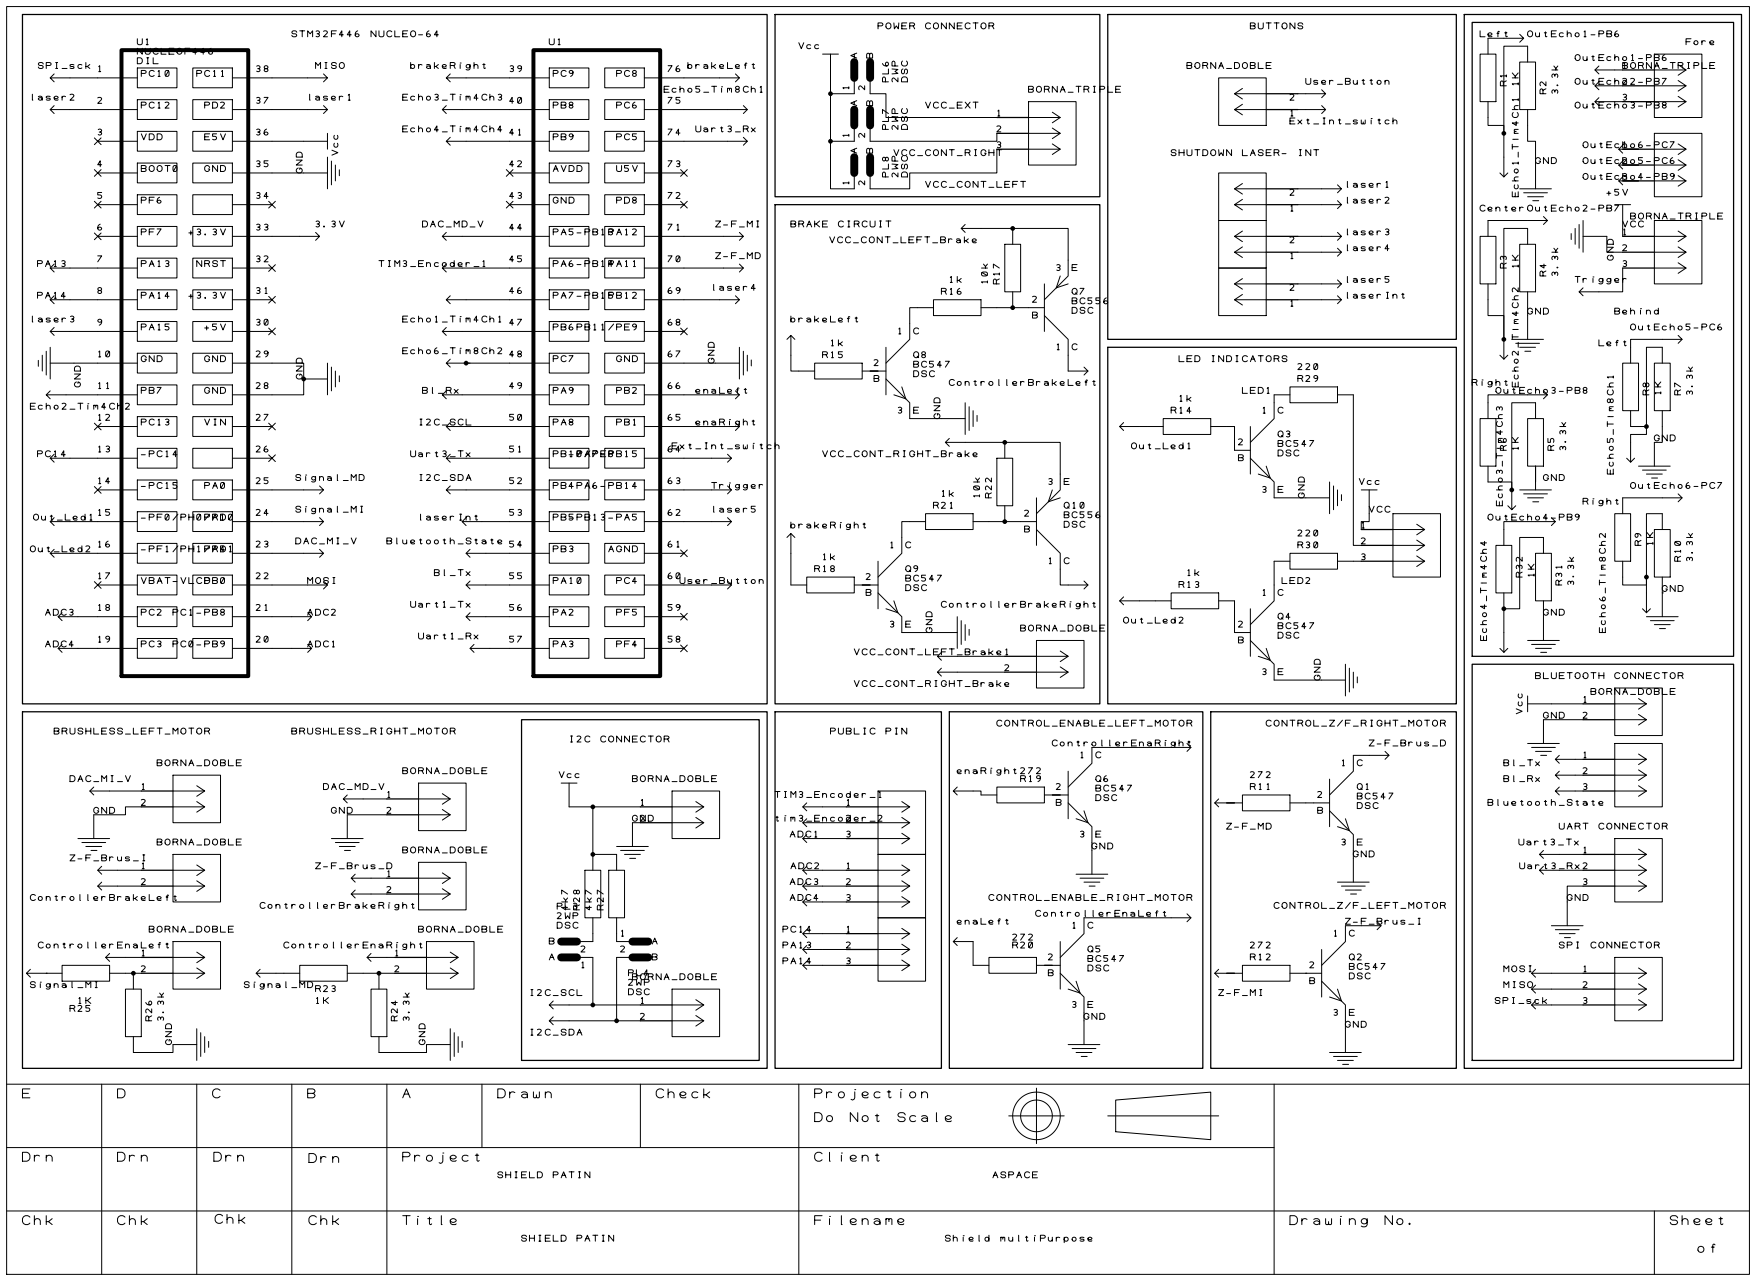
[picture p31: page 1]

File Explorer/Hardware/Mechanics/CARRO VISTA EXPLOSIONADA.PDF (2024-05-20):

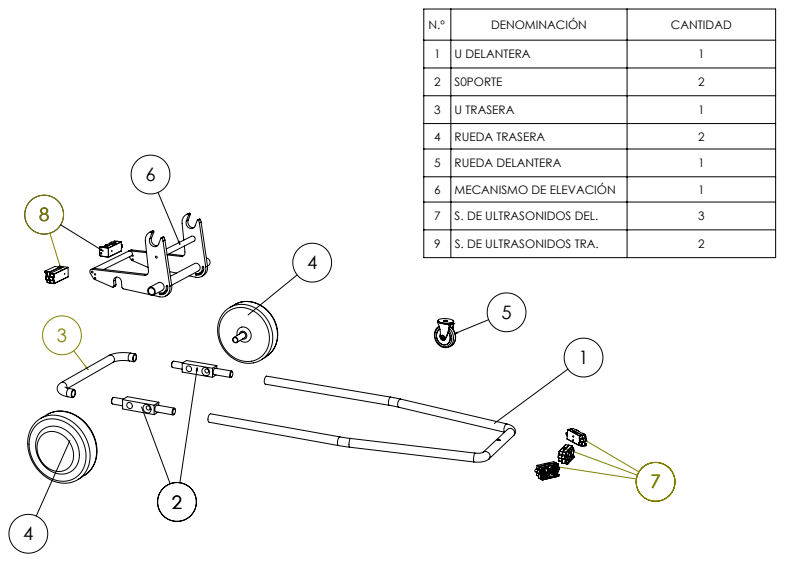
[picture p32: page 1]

N.º | DENOMINACIÓN | CANTIDAD
1 | U DELANTERA | 1
2 | S0PORTE | 2
3 | U TRASERA | 1
4 | RUEDA TRASERA | 2
5 | RUEDA DELANTERA | 1
6 | MECANISMO DE ELEVACIÓN | 1
7 | S. DE ULTRASONIDOS DEL. | 3
9 | S. DE ULTRASONIDOS TRA. | 2

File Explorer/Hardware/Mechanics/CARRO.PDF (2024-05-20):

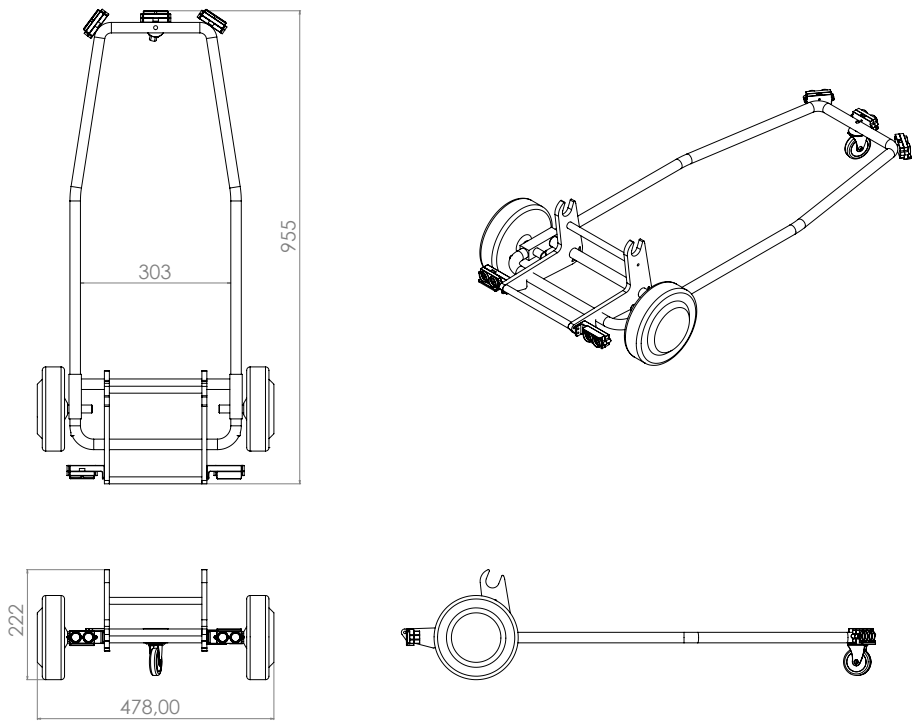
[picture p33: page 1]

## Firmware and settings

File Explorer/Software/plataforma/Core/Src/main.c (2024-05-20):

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
/* Includes ------------------------------------------------------------------*/
#include "main.h"

/* USER CODE BEGIN Includes */
/*Este archivo contiene, fundamentalmente, la configuración del hardware
 * del STM32 para el manejo de la Silla Exploradora, inicialización de algunas
 * variables, el gestor de tareas y la rutina HAL_IntTick que se ejecuta cada 1ms.
 *
 * En concreto, el hardware utilizado es:
 * USART1 Para la comunicación con el móvil a través de un enlace Bluetooth a 9600bps
 * USART2 Para la programación
 * USART3 Para el uso del DSPmp3 a una comunicación a 9600bps
 *
 * LEDS:
 * 	Amarillo: PA8
 * 		Continuo: Conectado a Bluetooth y Comenzar pulsado
 * 		Discontinuo Lento: Esperando botón Comenzar
 * 		Discontinuo Rápido: Sin conectar a Bluetooth
 * 	Verde: PB4
 *		Discontinuo Lento: Esperando pulsación
 *		Discontinua rápido: Marcha atrás
 *		Continuo: Marcha adelante
 *		Apagado: Esperando conexión y comenzar
 *
 *	Conector para pulsador adaptado: PC4
 *	Conector para deshabilitar ultrasonidos: PC3
 *	Controlador de motores
 *		Para cada uno de los motores, derecho e izquierdo, tenemos las
 *		siguientes señales
 *					R			L		tipo
 *		Enable		PB1			PB2		salida STM32
 *		dirección	PA11		PA12	salida STM32
 *		Brake		PC9			PC8		salida STM32
 *		Signal		PA0			PA1		entrada STM32
 *		DAC			PA5			PA4		salida STM32
 *
 *		El motor izquierdo tiene etiqueta 0, y el derecho, la 1
 *
 *	Convertidor DAC para el control de los motores
 *	Anillo de sensores de ultrasonidos.
 *		Cada sensor de ultrasonidos tiene dos terminales de control: Eco, Trigger
 *		Los sensores se enumeran de la siguiente forma. Situándonos desde la parte
 *		trasera de la plataforma, de izquierda a derecha, los sensores frontales
 *		son el 0,1,2 y los traseros, el 3 y 4
 *
 *		El trigger es común para los 5 ultrasonidos PB14
 *
 *				1	2	3	4	5
 *		Eco		PB6	PB7	PB8	PC6	PC7
 *
 *
 *	Se configuran Timers para el control del sistema
 *
 *	Timer2 -> Velocidad de los motores. 0 izquerda, 1 derecha, conectados
 *		a PA01 y PA1 respectivamente. Es timer de 32 bits, con prescaler de 83
 *		Channel 1 y 2 input capture RISING EDGE
 *	Timer12-> Generación de Trigger para los sensores de ultrasonidos
 *		Prescaler 83, period =60000, pulse =40, PWM1 Ch1, TriggerEvent=Update
 *		Auto-reload = enable
 *
 *	Timer4 -> Medición de pulsos para los ecos de los sensores delanteros (0,1,2)
 *		Prescaler 83, period=65535
 *		Ch1-> PB6,Input capture, BOTH EDGES
 *		Ch2-> PB7,Input capture, BOTH EDGES
 *		Ch3-> PB8,Input capture, BOTH EDGES
 *
 *	Timer8 -> Medición de pulsos para los ecos de los sensores traseros (3,4)
 *		Prescaler 83, period=65535
 *		Ch1 ICDM, BOTH EDGES
 *		Ch2 ICDM, BOTH EDGES
 *
 *
 * *
 *  */
#include "globales.h"



void InicializaVariables(void);
void GestorTareas(void);
/* USER CODE END Includes */

DAC_HandleTypeDef hdac;

TIM_HandleTypeDef htim2;
TIM_HandleTypeDef htim3;
TIM_HandleTypeDef htim4;
TIM_HandleTypeDef htim8;
TIM_HandleTypeDef htim12;

UART_HandleTypeDef huart1;
UART_HandleTypeDef huart2;
UART_HandleTypeDef huart3;
DMA_HandleTypeDef hdma_usart1_tx;
DMA_HandleTypeDef hdma_usart3_tx;

void SystemClock_Config(void);
static void MX_GPIO_Init(void);
static void MX_USART2_UART_Init(void);
static void MX_DMA_Init(void);
static void MX_USART1_UART_Init(void);
static void MX_DAC_Init(void);
static void MX_TIM2_Init(void);
static void MX_TIM3_Init(void);
static void MX_TIM12_Init(void);
static void MX_TIM8_Init(void);
static void MX_TIM4_Init(void);
static void MX_USART3_UART_Init(void);
/* USER CODE BEGIN 0 */
extern int16_t mandog[2]; // Para el control de los motores

/* USER CODE END 0 */

/**
  * @brief  The application entry point.
  * @retval int
  */
int main(void)
{
  /* USER CODE BEGIN 1 */
	//tick.tiempo = 0;
//	uint8_t user_input;
  /* USER CODE END 1 */

  /* MCU Configuration--------------------------------------------------------*/

  /* Reset of all peripherals, Initializes the Flash interface and the Systick. */
  HAL_Init();

  /* Configure the system clock */
  SystemClock_Config();

  /* Initialize all configured peripherals */
  MX_GPIO_Init();
  MX_USART2_UART_Init();
  MX_DMA_Init();
  MX_USART1_UART_Init();
  MX_DAC_Init();
  MX_TIM2_Init();
  MX_TIM3_Init();
  MX_TIM12_Init();
  MX_TIM8_Init();
  MX_TIM4_Init();
  MX_USART3_UART_Init();
  /* USER CODE BEGIN 2 */

  //Para el control del motor
  HAL_DAC_Start(&hdac, DAC_CHANNEL_1);
  HAL_DAC_Start(&hdac, DAC_CHANNEL_2);


  //Para la medida de los Hall
  HAL_TIM_IC_Start_IT(&htim2, TIM_CHANNEL_1);
  HAL_TIM_IC_Start_IT(&htim2, TIM_CHANNEL_2);


  //Para el trigger de los dispositivos de ultrasonidos
   HAL_TIM_PWM_Start(&htim12,TIM_CHANNEL_1);

   //Para los ecos de los ultrasonidos traseros
   HAL_TIM_IC_Start_IT(&htim8, TIM_CHANNEL_1);
   HAL_TIM_IC_Start_IT(&htim8, TIM_CHANNEL_2);

   //Ppara los ecos de los ultrasonidos delanteros
    HAL_TIM_IC_Start_IT(&htim4, TIM_CHANNEL_2);
    HAL_TIM_IC_Start_IT(&htim4, TIM_CHANNEL_3);
    HAL_TIM_IC_Start_IT(&htim4, TIM_CHANNEL_4);

  InicializaVariables();
 // bt_command='0';
  //HAL_UART_Receive_IT(&huart1, &bt_command, sizeof(uint8_t));
  /* USER CODE END 2 */

  /* Infinite loop */
  /* USER CODE BEGIN WHILE */
  //ActualizaVelocidad(-700,500);
  while (1)
  {
    /* USER CODE END WHILE */

    /* USER CODE BEGIN 3 */

/*		HAL_DAC_SetValue(&hdac, DAC_CHANNEL_1,DAC_ALIGN_12B_R , 1500);
		HAL_DAC_SetValue(&hdac, DAC_CHANNEL_2,DAC_ALIGN_12B_R , 1500);
*/
	GestorTareas();
/*
	if(com.bt_state)
		hard.leds=(LEDY_ON_1_DE_2 | LEDG_ON_1_DE_5);
	else
		hard.leds=(LEDY_OFF | LEDG_ON);
*/
	/*if(tick.tiempo == 4000)
	{

   	   ActualizaVelocidad(600,400);
	}
		if(tick.tiempo ==8000)
		{
		   	ActualizaVelocidad(0,0);
			tick.tiempo = 0;
		}

	DetectaMovimiento();
*/
/*
	HAL_DAC_SetValue(&hdac, 0,DAC_ALIGN_12B_R , 500);
	HAL_GPIO_WritePin(GPIOB, GPIO_PIN_2, GPIO_PIN_RESET);  //Disable
	//HAL_GPIO_WritePin(GPIOC, GPIO_PIN_9, GPIO_PIN_SET);  //Brake
	HAL_GPIO_WritePin(GPIOA, GPIO_PIN_12, GPIO_PIN_RESET); //Direction

	HAL_DAC_SetValue(&hdac, 16 ,DAC_ALIGN_12B_R , 500);
	HAL_GPIO_WritePin(GPIOB, GPIO_PIN_1, GPIO_PIN_RESET);  //Disable
	//HAL_GPIO_WritePin(GPIOC, GPIO_PIN_9, GPIO_PIN_SET);  //Brake
	HAL_GPIO_WritePin(GPIOA, GPIO_PIN_11, GPIO_PIN_SET); //Direction
*/



  }
  /* USER CODE END 3 */
}

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
/* USER CODE BEGIN 4 */
void HAL_IncTick(void)
{
	/*Esta función se ejecuta cada 1ms. Contiene el incremento de las variables
	 * globales que se usan en cada una de las tareas*/
	uint8_t i;


	tick.tiempo++;   //Para el control de la navegación
					 //Esta variable controla el tiempo que está operando la silla
					 //entre pulsaciones
	tick.tiempo_backward++; //Para el control de la navegación
					//Este tiempo se utiliza para controlar el tiempo de la marcha atrás

	/* t_blink se usa para la activación intermitente de los leds
	 * Cada ms se incrementan estas variables
	 * */
	for(i=0;i<2;i++)
		tick.t_blink[i]+=1;

	/*Para el pulsador, eliminar el rebote*/
	tick.t_rebote++;

	/*Para el pulsador que habilita el eco, eliminar el rebote*/
	tick.t_rebote_pul_eco++;


	/*Las variables tiempo_temporal_med y tiempo_med se utilizan paras
	 * el protocolo de comunicaciones. La primera establece intervalos de
	 * 100ms y la segunda se incrementa cada 100ms. Es la información que
	 * se envía con cada paquete de datos a la aplicación de Alejandro*/
	tick.tiempo_temporal_med+=1;
	if (tick.tiempo_temporal_med==100)
	{
			tick.tiempo_temporal_med=0;
			tick.tiempo_med+=1;
	}

	tick.t_dac++; //Establece el tiempo para el cual se ejecuta la rutina de control de motores

	/*Las siguientes medidas permiten actualizar la velocidad
	 * de las ruedas cuando están paradas. Si transcurre más de 300ms
	 * sin una medida nueva en el hall, las ruedas están paradas.
	 * Se pone hall[i] a su valor más alto y se activa la señal medida
	 * nueva_hall[i]
	 * */
	for(i=0;i<2;i++)
	{
		tick.t_med_hall[i]+=1;
		if(tick.t_med_hall[i]>300)
		{
			tick.t_med_hall[i]=0;
			hall[i]=4294967295;
			medida_nueva_hall[i]=1;
		}
	}

	//Establece un tiempo mínimo para cambiar de estado y evitar secuencias
	state.tiempo_estado++;

	//audio.tiempo++;

	/*Para la función de control de motores. Se necesitan algunos delays
	 * que se gestionan en estas variables*/
	for(i=0;i<2;i++)
	{
		tmotor.t_arranque[i]+=1;
		tmotor.t_delay_pid[i]+=1;
	}

	//Algunos delays son necesarias para el envío de
	//los comandos durante el proceso de inicialización
	audio.tiempo++;

}

void InicializaVariables(void)
{
	  uint8_t i;
	  tick.tiempo=0;
	  tick.tiempo_backward=0;
	  tick.t_dac=0;
	  tick.tiempo_temporal_med=0;
	  tick.tiempo_med=0;
	  for(i=0;i<2;i++)
		  tick.t_med_hall[i]=0;

	  par.tiempo=TIEMPO_MOV;
	  par.tiempo_rotate = TIEMPO_ROT;
	  par.tiempo_atras = TIEMPO_ATRAS;
	  par.vel=VEL;
	  par.obs_near=DISTANCIA_OBSTACULO_1;
	  par.obs_far=DISTANCIA_OBSTACULO_2;
}



void GestorTareas(void)
{
	/*  Esta función es el núcleo del programa de la Silla Exploradora.
	 *  Llama en bucle sin fin a cada una de las tareas. Se debe tener
	 *  en cuenta que ninguna de ellas puede ser bloqueante para la correcta
	 *  ejecución del conjunto.
	 *
	 * */

	GestorMotores();
	GestorComunicaciones();
	GestorSensores();
	GestorInterfaz();
	Navegacion();
	GestorAudio();
}

/* USER CODE END 4 */
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


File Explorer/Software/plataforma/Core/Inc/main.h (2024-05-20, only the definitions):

#define Dis_eco_Pin GPIO_PIN_3
#define Dis_eco_GPIO_Port GPIOC
#define USART_TX_Pin GPIO_PIN_2
#define USART_TX_GPIO_Port GPIOA
#define USART_RX_Pin GPIO_PIN_3
#define USART_RX_GPIO_Port GPIOA
#define User_button_Pin GPIO_PIN_4
#define User_button_GPIO_Port GPIOC
#define Enable_R_Pin GPIO_PIN_1
#define Enable_R_GPIO_Port GPIOB
#define Enable_L_Pin GPIO_PIN_2
#define Enable_L_GPIO_Port GPIOB
#define Trigger_Pin GPIO_PIN_14
#define Trigger_GPIO_Port GPIOB
#define Brake_L_Pin GPIO_PIN_8
#define Brake_L_GPIO_Port GPIOC
#define Brake_R_Pin GPIO_PIN_9
#define Brake_R_GPIO_Port GPIOC
#define Led_amarillo_Pin GPIO_PIN_8
#define Led_amarillo_GPIO_Port GPIOA
#define Z_F_R_Pin GPIO_PIN_11
#define Z_F_R_GPIO_Port GPIOA
#define Z_F_L_Pin GPIO_PIN_12
#define Z_F_L_GPIO_Port GPIOA
#define TMS_Pin GPIO_PIN_13
#define TMS_GPIO_Port GPIOA
#define TCK_Pin GPIO_PIN_14
#define TCK_GPIO_Port GPIOA
#define BT_State_Pin GPIO_PIN_3
#define BT_State_GPIO_Port GPIOB
#define Led_verde_Pin GPIO_PIN_4
#define Led_verde_GPIO_Port GPIOB

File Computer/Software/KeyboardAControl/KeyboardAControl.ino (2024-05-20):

/*
  KeyboardAndMouseControl

 Controls the mouse from five pushbuttons on an Arduino Leonardo, Micro or Due.

 Hardware:
 * 5 pushbuttons attached to D2, D3, D4, D5, D6

 The mouse movement is always relative. This sketch reads
 four pushbuttons, and uses them to set the movement of the mouse.

 WARNING:  When you use the Mouse.move() command, the Arduino takes
 over your mouse!  Make sure you have control before you use the mouse commands.

 created 15 Mar 2012
 modified 27 Mar 2012
 by Tom Igoe

 this code is in the public domain

 */

#include "Keyboard.h"
#include "Mouse.h"
/*
  Programa para la gestión del ordenador durante el experimento de la causa-efecto en ASPACE
  El sistema necesita estar conectado con la aplicación Bluetooth de Alex
  Cuando se le da a comenzar en dicha aplicación, recibe un comando GO, que transmite a su vez para
  identificar el momento de comienzo. El stop para el funcionamiento y manda el mensaje ST hacia 
  la aplicación. Con ello se sabe, en todo momento cuándo comienza y finaliza el ensayo.

  Existe un pulsador de cuidador y un pulsador de usuario. El pulsador del cuidador se presiona para
  sincronizar la aplicación con Youtube, una vez que se ha iniciado el ensayo (recepción comando GO)
  C0,tiempo,x, y P0,tiempo,x y P1,tiempo,x, junto con el tiempo son los mensajes que se reciben.
  Junto con el mensaje C0,tiempo,x, se manda un mensaje de estado, indicando en cuál está, pero sin
  alterarlo. Tanto el pulsador del cuidador como el del usuario, generan la transmisión de la constante 'k'
  para reproduccir o parar youtube.

  También se transmiten mensajes relacionados con el estado del Arduino, con el formato Sn,tiempo,x, donde
  n puede ser 0,1 y 2. En el estado S2, el Arduino está esperando una pulsación para poner en marcha el video.
  Durante la reproducción del vídeo, el Arduino está en el estado S1 que debe terminar una vez transcurrido
  el tiempo de exposición. Por consiguiente, el tiempo entre S2 y P0 identifica el tiempo de reacción, mientras
  que las pulsaciones P0-P1 durante S1 representan errores de pulsación.   

  Estados y eventos en el computador:

  
              |-----------------|      
  ------------|                 |------------------
  S2           S1                S2 
            

  S2: Espera a pulsación. Youtube parado
  S1: Reproducción Youtube durante tiempo estipulado
  P0: Pulsación usuario
  P1: Liberación usuario
  C0: Pulsación cuidador para sincronismo con ordenador

  Tiempo de reacción: Tiempo desde la transición S1-S2 a la pulsación P0
  Errores de comisión: Secuencias P0-P1 durante el estado S1
  
*/



//Tiempo de exposicion en ticks de 0.1 segundos
#define TIEMPO_EXPOSICION 300 
#define STOP 0X40
#define GO 0XF0

//Comentar la siguiente línea si no se quiere mandar los comandos al terminal
#define DEBUG 

// set pin numbers for the five buttons:
const int InternalButton = A1;
const int ExternalJack = 5;
const int BluetoothState = 2;
const int ledPin =  13; 

int valor=0;
unsigned long myTimeP;
unsigned long tick;
unsigned int tiempo_exposicion;
int state = LOW;


void setup() { // initialize the buttons' inputs:
  pinMode(InternalButton, INPUT_PULLUP);
  pinMode(ExternalJack, INPUT_PULLUP);
  pinMode(BluetoothState, INPUT);
  // initialize the LED pin as an output:
  pinMode(ledPin, OUTPUT);
  Serial.begin(9600);
  Serial1.begin(9600);
  // initialize mouse control:
//  Mouse.begin();
  Keyboard.begin();
  myTimeP = millis();
  tick = 0; 
  state = digitalRead(ExternalJack);
  tiempo_exposicion=0;
  //Serial1.println('Hola');
}


void loop(){
  static unsigned long old_tick;
  static unsigned char run;  //Tres estados inicio, run, stop
  int botonusu,botoncuidador;
  char buffer[5];
  unsigned char a;
  char pulsacion=0;
  char pulsacion_cuidador=0;
  static char state_cuidador;
  
  unsigned long myTime = millis();  //Actualizamos los milisegundos
  if( (myTime-myTimeP)>=100)
  {  
  
    tick++;
    myTimeP = myTime;  
    if(tiempo_exposicion>0)
      tiempo_exposicion--;
    /* La variable tick se debe actualizar cada 100ms.
    */ 
   }

   if(Serial1.available()>0)
   {
      a=Serial1.read();
      #ifdef DEBUG
      Serial.println(a,HEX);
      #endif
      if(a == GO )
      {
          buffer[0]='G';
          buffer[1]='0';
          buffer[2]=',';
          buffer[3]=0;
          Serial1.print(buffer);
          Serial1.print(tick);
          Serial1.print('x');
          #ifdef DEBUG
          Serial.print(buffer);
          Serial.print(tick);
          Serial.print('x');
          #endif
              run=1;
              tiempo_exposicion = TIEMPO_EXPOSICION;
              Keyboard.write('k');
      } else            
      if(a == STOP)
      {
          buffer[0]='S';
          buffer[1]='T';
          buffer[2]=',';
          buffer[3]=0;
          Serial1.print(buffer);
          Serial1.print(tick);
          Serial1.print('x');
          #ifdef DEBUG
          Serial.print(buffer);
          Serial.print(tick);
          Serial.print('x');
          #endif
          if(run!=0)
          {
            run=0;
            tiempo_exposicion=0;
            Keyboard.write('k');
          }
       }
    }

  if( (tick -old_tick)>=2)
  {
    /* Cada 200ms se lee el pulsador externo para evitar rebotes*/
    old_tick = tick;
  //  Serial1.println(tick);
    botonusu= digitalRead(ExternalJack);
    botoncuidador = digitalRead(InternalButton);
  //  digitalWrite(ledPin,botonusu);
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

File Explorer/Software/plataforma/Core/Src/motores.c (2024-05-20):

/*
 * motores.c
 *
 *  Created on: Nov 30, 2022
 *      Author: alber
 */


#include "globales.h"
#include "main.h"


void ControlMotores(void);
void GestorMotores(void);
void ActualizaVelocidad( int16_t  izq, int16_t der);


extern DAC_HandleTypeDef hdac;
//extern float consigna;

int16_t mandog[2]; // Para el control de los motores



GPIO_TypeDef *port_disable=GPIOB;
GPIO_TypeDef *port_direction=GPIOA;
GPIO_TypeDef *port_brake=GPIOC;


uint16_t pin_disable_motor[2]={GPIO_PIN_2,GPIO_PIN_1}; //Array con la información de los pines asociados a los pines que manejan el enable de los controladores de motor.
uint16_t pin_direction_motor[2]={GPIO_PIN_12,GPIO_PIN_11}; //Array con la información de los pines asociados a los pines que manejan el enable de los controladores de motor.
uint16_t pin_brake_motor[2]={GPIO_PIN_8,GPIO_PIN_9}; //Array con la información de los pines asociados a los pines que manejan el enable de los controladores de motor.
uint16_t pin_salida_motor[2] = {DAC_CHANNEL_1,DAC_CHANNEL_2};


void ActualizaVelocidad( int16_t  izq, int16_t der)
{

	vel[IZQUIERDO] = izq;
	vel[DERECHO] = der;
	consigna[IZQUIERDO] = (float)izq * consigna_vmax/VEL;
	consigna[DERECHO] = (float)der * consigna_vmax/VEL;

	//mandoglobal[IZQUIERDO]=izq/400;
	//mandoglobal[DERECHO] = der/400;

}


void GestorMotores(void)
{
	/*
	 * Función no bloqueante para el control de los motores
	 * */

	static uint8_t inicio;
	if(inicio==0)
	{
		inicio=1;
		ResetPID(0);
		ResetPID(1);
	}

	/*El Gestor de Motores llama cada 40ms al ControlMotores, que actualiza */
	if(tick.t_dac==40)
	{
		ControlMotores();
		tick.t_dac=0;
	}

}

void ResetPID(uint8_t n)
{
		pid[n].ed=0;
		pid[n].ei=0;
		pid[n].ep=0;
}



int16_t Algoritmo_PID(float vel_medida, float vel_consigna, uint8_t m )
{
	int16_t mando;
	float dif;
	pid[m].ep = vel_consigna-vel_medida;
	dif = pid[m].ep - pid[m].ed;
	mando = (int16_t) (Kp*pid[m].ep + Kd*dif + Ki*pid[m].ei);
	pid[m].ep = dif;
	if(mando <= VEL_MAX )
		pid[m].ei += pid[m].ep;

	if(mando<200)
		mando=200;
	else if(mando >VEL_MAX)
		mando = VEL_MAX ;
	return mando;
}


void ControlMotores(void)
{
	/*Esta función integra el PID con la operación de motor, se ejecuta cada 40ms*/

	#define TIEMPO_DESCONEXION_ARRANQUE 400
	//#define TIEMPO_DESCONEXION 3000
	#define MANDO_TRANSICION 500
	#define PALANTE GPIO_PIN_RESET
	#define PATRAS GPIO_PIN_SET


	/**********************************************************
	 * Información de la máquina de estados que gobierna el control
	 * de motores sin PID
	 * Nomenclatura:
	 * - Sx: nombre de estado
	 * 		Entrada(Valor): Próximo estado /Acción
	 * Nota: i-> 0 motor izquierdo,  1 motor derecho
	 * ********************************************************
	 *  S0: MOTOR PARADO
	 * 		vel[i] (>0) : S1 / t_arranque[i]=0, disable_motor[i] = 1, brake_motor[i]=0 ;
	 * 		vel[i] (<0) : S11 / t_arranque[i]=0, disable_motor[i] = 1, brake_motor[i]=0;
	 *      o.c : S0, disable_motor[i] = 1, brake_motor[i]=0 ;
	 *  S1: MOTOR ESPERA ADELANTE
	 *		vel[i] (==0) : S1 / disable_motor[i] = 1, brake_motor[i]=0 ;
	 *		t_arranque[i] (> Umbral) : S2 / mandog[i] = vel[i], disable_motor[i] = 1, brake_motor[i]=0 ;
	 * 		o.c : S1: disable_motor[i] = 1, brake_motor[i]=0 ;
	 *  S2: MOTOR ADELANTE
	 *  	vel[i] (==0) : S3 / mandog[i] = vel[i], direccion_motor[i]= AVANCE, disable_motor[i] = 0, brake_motor[i]=0 ;
	 * 		vel[i] (<0)  : S12	/ mandog[i] = vel[i], direccion_motor[i]= AVANCE, disable_motor[i] = 0, brake_motor[i]=0 ;
	 * 		o.c			 : S2 / / mandog[i] = vel[i], direccion_motor[i]= AVANCE, disable_motor[i] = 0, brake_motor[i]=0 ;
	 * 	S3: FRENADA
	 * 		sensor.freq[i] (<UMBRAL) : S1 / mandog[i]=0, brake_motor[i]=1;
	 * 		sensor.freq[i] (>UMBRAL) : S3 / mandog[i]=0, brake_motor[i]=1;
	 * 		oc : S3 / mandog[i]=0, brake_motor[i]=1;
	 * 	S11: MOTOR ESPERA ATRAS
	 *		vel[i] (==0) : S1 / disable_motor[i] = 1, brake_motor[i]=0 ;
	 *		t_arranque[i] (> Umbral) : S12 / mandog[i] = -vel[i], disable_motor[i] = 1, brake_motor[i]=0 ;
	 * 		o.c : S11: disable_motor[i] = 1, brake_motor[i]=0 ;
	 *  S12: MOTOR ATRAS
	 *  	vel[i] (==0) : S3 / mandog[i] = -vel[i], direccion_motor[i]= ATRAS, disable_motor[i] = 0, brake_motor[i]=0 ;
	 * 		vel[i] (>0)  : S2	/ mandog[i] = -vel[i], direccion_motor[i]= ATRAS, disable_motor[i] = 0, brake_motor[i]=0 ;
	 * 		o.c			 : S12 / / mandog[i] = -vel[i], direccion_motor[i]= ATRAS, disable_motor[i] = 0, brake_motor[i]=0 ;
	 *
	 *
	 */



	static  uint8_t marcha[2];
	//marchag[0] = marcha[0];
	//marchag[1] = marcha[1];

	uint8_t i;
		//Marcha puede tomar losadelante 0
		//Marcha atrás 1

		for(i=0;i<2;i++)
		{
			switch(marcha[i])
			{
			case 0: if(vel[i]>0)
					{
						marcha[i]=1;
						tmotor.t_arranque[i]=0;
					};
					if(vel[i]<0)
					{
						marcha[i]=11;
						tmotor.t_arranque[i]=0;
					}
					HAL_GPIO_WritePin(GPIOB , pin_disable_motor[i], GPIO_PIN_SET);
					HAL_GPIO_WritePin(port_brake, pin_brake_motor[i], GPIO_PIN_RESET);
					mandog[i]=0;
				break;
			case 1: if(vel[i]==0)
						marcha[i]=0;
					else
						if(tmotor.t_arranque[i]>=TIEMPO_DESCONEXION_ARRANQUE)
						{
							marcha[i]=2;
							ResetPID(i);
							tmotor.t_delay_pid[i]=0;
						}
					HAL_GPIO_WritePin(port_disable, pin_disable_motor[i], GPIO_PIN_SET);
					HAL_GPIO_WritePin(port_direction, pin_direction_motor[i], PALANTE);
					HAL_GPIO_WritePin(port_brake, pin_brake_motor[i], GPIO_PIN_RESET);
					mandog[i]=vel[i];
					break;
			case 2:
				HAL_GPIO_WritePin(port_disable,pin_disable_motor[i],GPIO_PIN_RESET);
				HAL_GPIO_WritePin(port_direction, pin_direction_motor[i], PALANTE);
				HAL_GPIO_WritePin(port_brake, pin_brake_motor[i], GPIO_PIN_RESET);
				/*if(vel[i]<=0)
					marcha[i]=3;*/
				if(vel[i]==0)
					marcha[i]=3;
				if(vel[i]<0)
				{	//marcha[i]=0; //Lo paso por el estado cero para que se rearme los controladores
					marcha[i]=12; //Lo que había antes
					ResetPID(i);
					tmotor.t_delay_pid[i]=0;
				}
				if(vel[i]>0)
				{
					if(tmotor.t_delay_pid[i]<2200)
						mandog[i]=vel[i];
					else
	//				mandog[i]=vel[i];
						mandog[i] = Algoritmo_PID(sensor.frequency[i], consigna[i], i);
				};
				break;
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

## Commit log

2024-05-20 Files to replicate a study to show the effect of mobility on cognitive skills in children with cerebral palsy
    [PatinAspace - Bottom Copper (Paste).gbr, PatinAspace - Bottom Copper (Resist).gbr, PatinAspace - Bottom Copper.gbr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]
2024-05-20 Updated 20-4
    [PatinAspace - Bottom Copper (Paste).gbr, PatinAspace - Bottom Copper (Resist).gbr, PatinAspace - Bottom Copper.gbr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]

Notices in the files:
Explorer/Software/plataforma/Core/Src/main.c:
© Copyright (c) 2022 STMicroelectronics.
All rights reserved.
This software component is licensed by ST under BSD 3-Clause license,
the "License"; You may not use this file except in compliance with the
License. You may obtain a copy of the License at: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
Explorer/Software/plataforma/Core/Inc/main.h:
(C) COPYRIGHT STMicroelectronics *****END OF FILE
